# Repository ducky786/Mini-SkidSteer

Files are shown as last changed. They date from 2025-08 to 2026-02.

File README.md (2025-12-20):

# DESK TOP SKIDSTEER

My project is a small RC skidsteer for the desktop to cure bordom. This Skidsteer is around 80mm x 70mm with a arm that includes a bucket tilt. The arm and the Tilt are powered by servos while the drive bace is powered by 2 N20 motors. The 
I wanted to build this beucase I found an intrest in these small desktop toys that could be fun to kill time on your desk. I went for a skidsteer because it would consist of something more then just simply driving around on top of your desk.  Like picking up small
things and throwing them around. Another reason I wanted to build this was beucase I also wanted to learn something new! During this build I have defenetly learn a significant amound of cad and PCB design! But the main reason is to have pure fun with a mini constuction vehicel!! 
# CAD:





The wheels are place holders for a 26mm D-ring Wheels: [Wheels](https://www.amazon.com/10pcs-D-Hole-Rubber-Wheel-Suitable/dp/B0DHS12GDV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)

# PCB:





# Wire-ring Diagram:



# FIRMWARE:



# BOM:

| Part | Quantity | Price  | Link |
|---|---|---|---|
| N20 Motors | 2(comes with 3) | $9.99  | https://www.amazon.com/Acxico-Micro-Motor-3V-6V-Gearbox/dp/B09DG3GCGK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 |
| Buck Converter | 1 | $1.33  | https://www.aliexpress.us/item/3256809224651081.html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 |
| DRV8833 | 1 | $2.24  | https://www.aliexpress.us/item/3256806906685301.html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"order"%3A"12"%2C"eval"%3A"1"%7D&pdp_npi=4%40dis%21USD%215.74%212.24%21%21%2141.08%2116.03%21%402103244617539962038712743e4150%2112000039378712005%21sea%21US%216395794669%21X&curPageLogUid=tkZwLZppvI4E&utparam-url=scene%3Asearch%7Cquery_from%3A&search_p4p_id=2025073114100314644857276615300003037063_2 |
| Servos sg90 | 2 | $3.98  | https://www.aliexpress.us/item/3256805909602108.html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"order"%3A"42"%2C"eval"%3A"1"%7D&pdp_npi=4%40dis%21USD%211.99%211.99%21%21%2114.27%2114.27%21%402103244817539963500562681e2fa1%2112000035720830774%21sea%21US%216395794669%21X&curPageLogUid=MTCLJAN4xnVc&utparam-url=scene%3Asearch%7Cquery_from%3A&search_p4p_id=20250731141230268300773175950003082043_1 |
| Wheels | 4(comes in 10)  | $6.73  | https://www.amazon.com/10pcs-D-Hole-Rubber-Wheel-Suitable/dp/B0DHS12GDV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 |
| Xiao ESP-32 | 1 | $4.43  | https://www.aliexpress.us/item/3256806898073871.html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"order"%3A"667"%2C"eval"%3A"1"%7D&pdp_npi=4%40dis%21USD%217.93%214.43%21%21%2156.74%2131.69%21%402103246617539966920224373e09d8%2112000039345574623%21sea%21US%216395794669%21X&curPageLogUid=fVxbMNHtmWwP&utparam-url=scene%3Asearch%7Cquery_from%3A&search_p4p_id=202507311418121917005778551220003052960_1 |
| XT30 | 1 | $1.99  | https://www.aliexpress.us/item/3256808022842675.html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"order"%3A"868"%2C"eval"%3A"1"%7D&pdp_npi=4%40dis%21USD%213.36%211.99%21%21%2124.07%2114.26%21%402101ea8c17539968895486921e633c%2112000044241722915%21sea%21US%216395794669%21X&curPageLogUid=UwLOdHYcZP7Q&utparam-url=scene%3Asearch%7Cquery_from%3A&search_p4p_id=202507311421295032891313211630003124381_5 |
| Pin Headers | 1 | $2.79  | https://www.aliexpress.us/item/3256805730789728.html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"order"%3A"45"%2C"eval"%3A"1"%7D&pdp_npi=4%40dis%21USD%212.97%212.79%21%21%2121.23%2119.96%21%402101c80217539969536874429edd11%2112000034840648426%21sea%21US%216395794669%21X&curPageLogUid=ouSfWTDoT1n5&utparam-url=scene%3Asearch%7Cquery_from%3A&search_p4p_id=202507311422337454539819102040003087391_2 |
| Female Header | 1 | $0.72  | https://www.aliexpress.us/item/2251832677159829.html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"order"%3A"5"%2C"eval"%3A"1"%7D&pdp_npi=4%40dis%21USD%210.76%210.72%21%21%210.76%210.72%21%402101c5bf17539970477882420ed5c5%2165355679105%21sea%21US%216395794669%21X&curPageLogUid=lampIYBHwC27&utparam-url=scene%3Asearch%7Cquery_from%3A |
| Screw Terminal | 1 | $3.24  | https://www.aliexpress.us/item/3256804481581777.html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"order"%3A"238"%2C"eval"%3A"1"%7D&pdp_npi=4%40dis%21USD%212.84%211.99%21%21%212.84%211.99%21%402101c59817539971308151068e26ea%2112000030040613013%21sea%21US%216395794669%21X&curPageLogUid=c4xiFsyJKPl5&utparam-url=scene%3Asearch%7Cquery_from%3A&search_p4p_id=2025073114253012899010225579360003107920_1 |
| TATTU lipo | 1 | $15.99 | Amazon.com: Gens ace 7.4V 450mAh 2S LiPo Battery Pack 25C/50C with JST Plug for Emax Babyhawk RC Heli 250 Helicopter Small Airplane Micro FPV Racing Drone Quadcopter : Toys & Games |
| Motor Mount | 2 | $6.49  | https://www.amazon.com/MECCANIXITY-Mounting-Bracket-11-5mm-Screws/dp/B09NN6FQ78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 |
| 3D Print Shipping | | ~$10 | |
| PCB | 1 | ~$15 | |
| TOTAL | | 79.92  | |

# FINAL PRODUCT:

This is the final PCB design! I feel that it came out Great and what I love about this PCB is that I can remove it from the Skidsteer and place it into a 3d printed car! I plan on using this it on other projects.




Now the skidseer interms of CAD, it came out great too. There defenety have been some bad tolerences and alignment but it came together well enough.

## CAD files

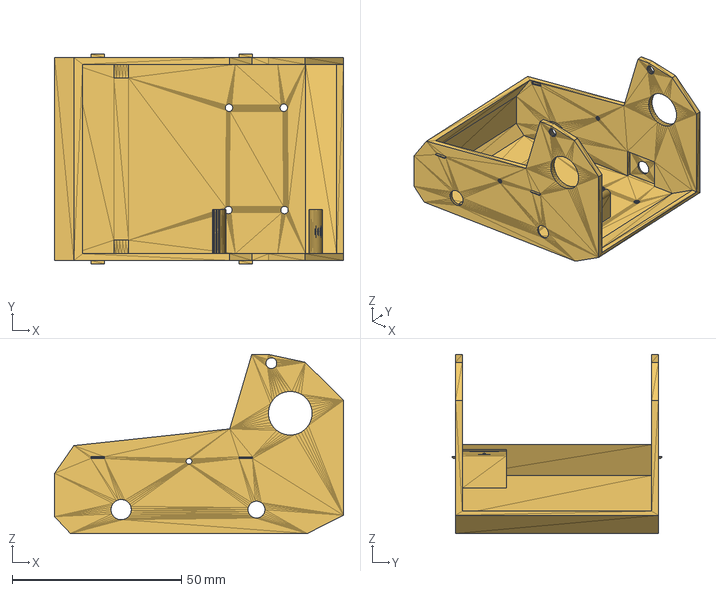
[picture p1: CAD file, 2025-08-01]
CAD/Body.step
85.4 x 62.0 x 53.0 mm

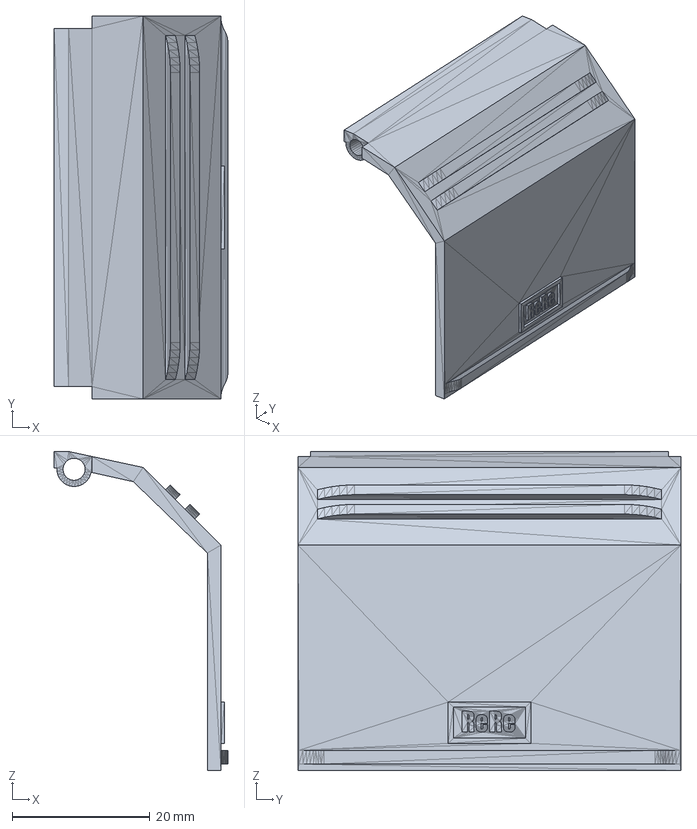
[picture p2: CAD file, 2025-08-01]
CAD/Back Cover.step
25.2 x 55.6 x 46.3 mm

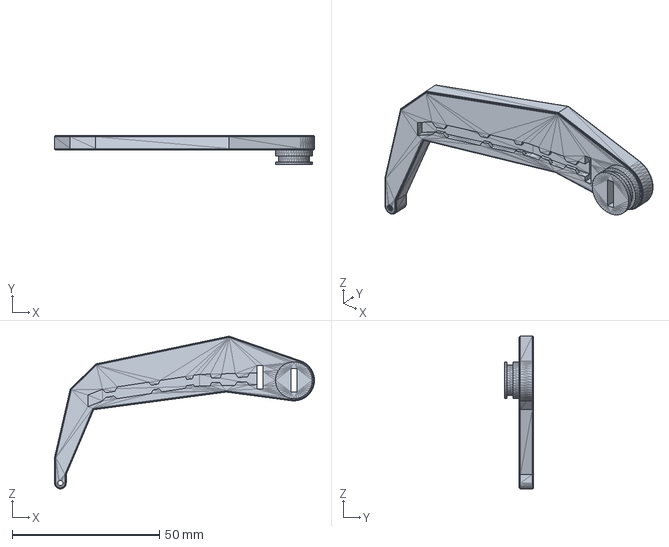
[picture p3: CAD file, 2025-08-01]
CAD/Right Arm.step
88.3 x 10.0 x 51.9 mm

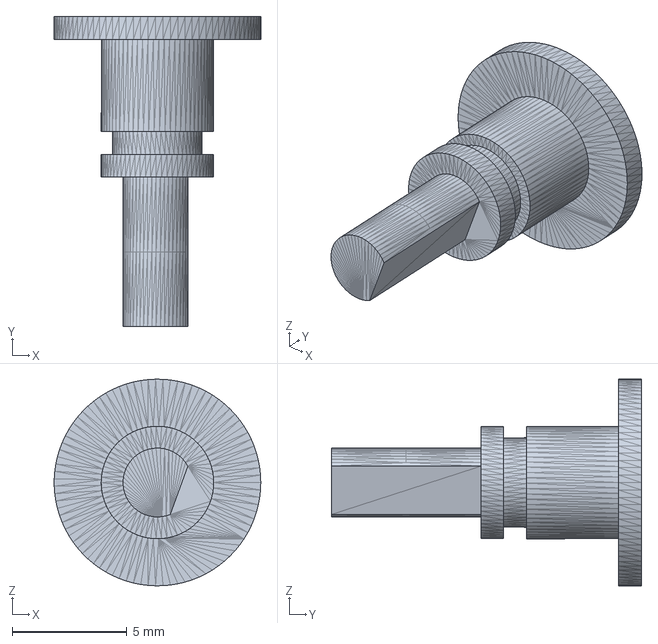
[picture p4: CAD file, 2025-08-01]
CAD/Axel.step
9.00 x 13.5 x 9.00 mm

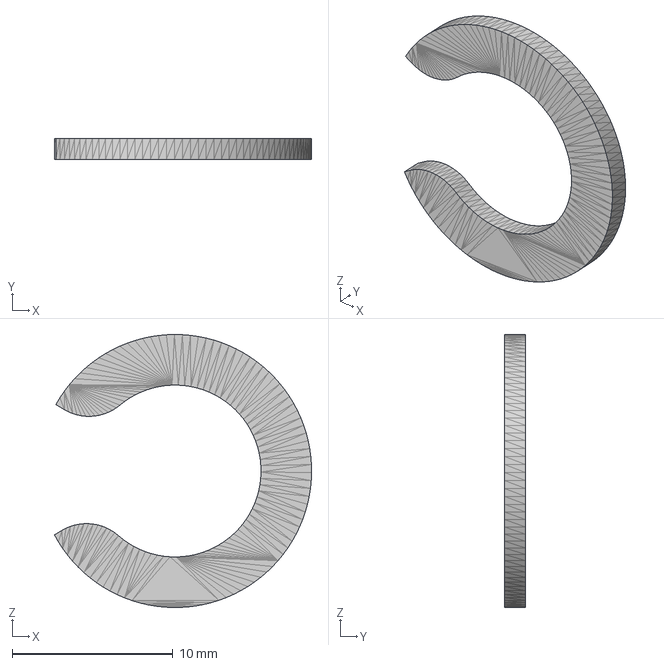
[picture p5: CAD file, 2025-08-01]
CAD/Arm C-Clip.step
16.0 x 1.30 x 17.0 mm

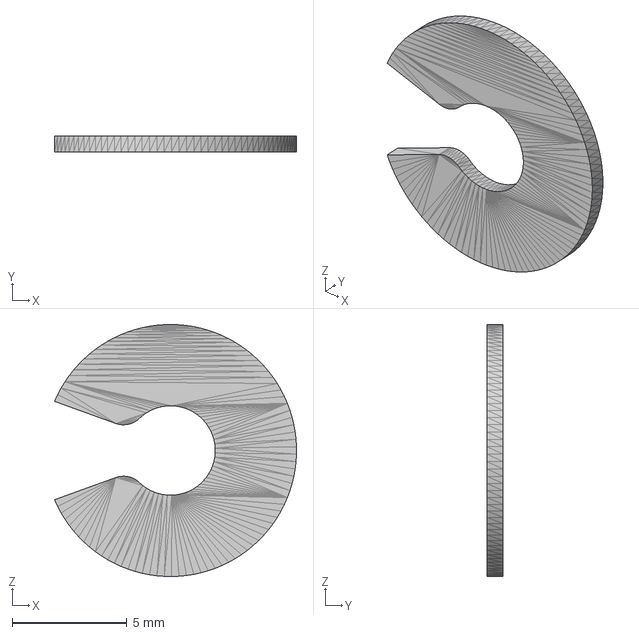
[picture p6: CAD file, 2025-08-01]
CAD/Axel C-Clips.step
10.6 x 0.7 x 11.0 mm

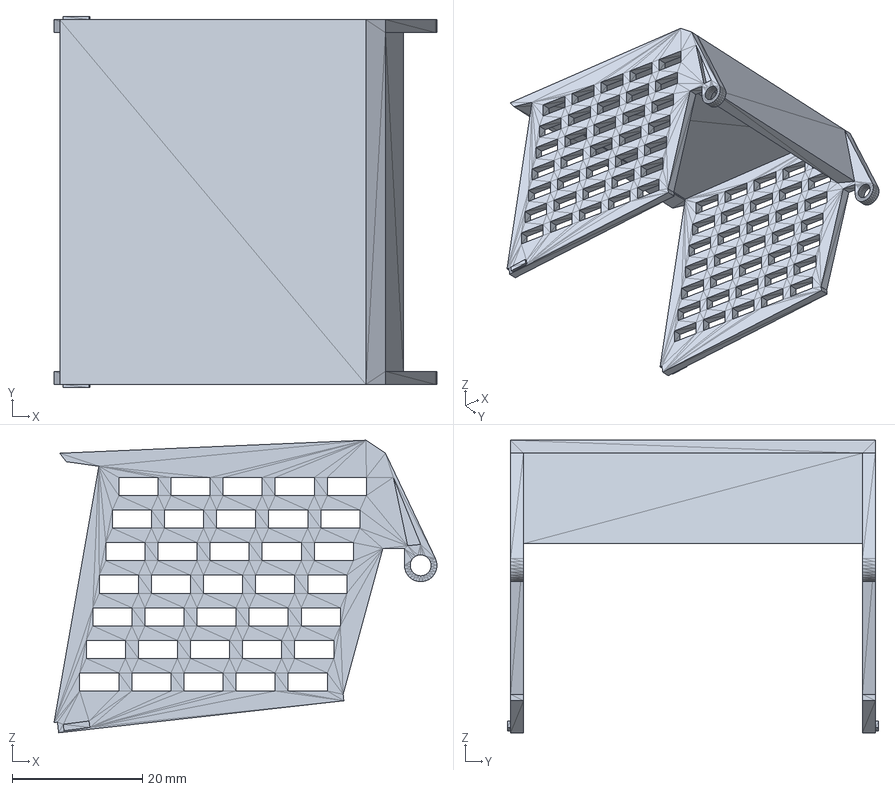
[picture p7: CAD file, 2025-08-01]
CAD/Driver Cab.step
58.8 x 57.0 x 44.9 mm

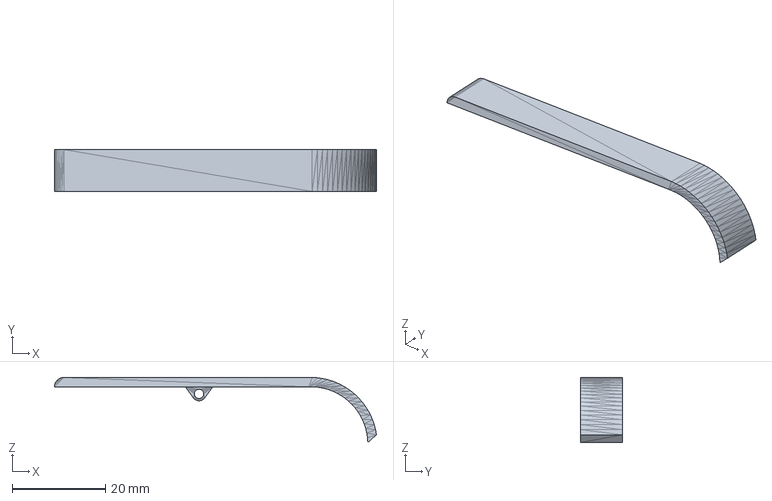
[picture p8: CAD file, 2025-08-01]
CAD/Left Wheel Cover.step
69.2 x 9.00 x 14.0 mm

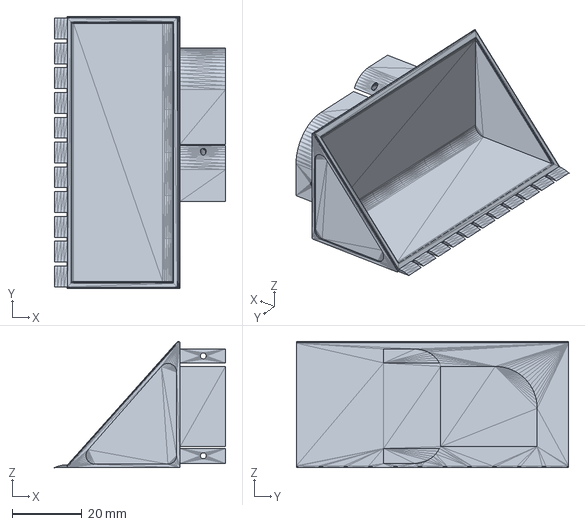
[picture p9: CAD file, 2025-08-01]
CAD/Bucket.step
49.0 x 78.0 x 36.2 mm

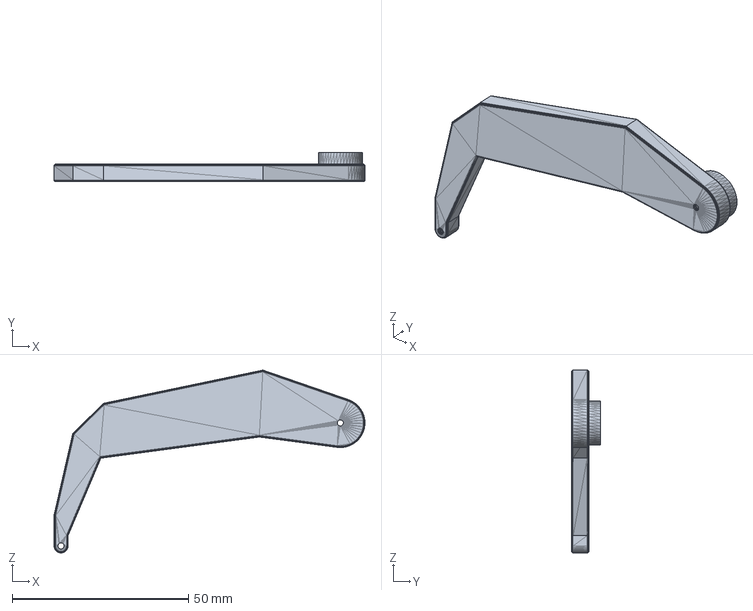
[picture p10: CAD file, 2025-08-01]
CAD/Left Arm.step
88.3 x 8.30 x 51.9 mm

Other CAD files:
CAD/Right Wheel Cover.step
CAD/Axel C-Clip E.step

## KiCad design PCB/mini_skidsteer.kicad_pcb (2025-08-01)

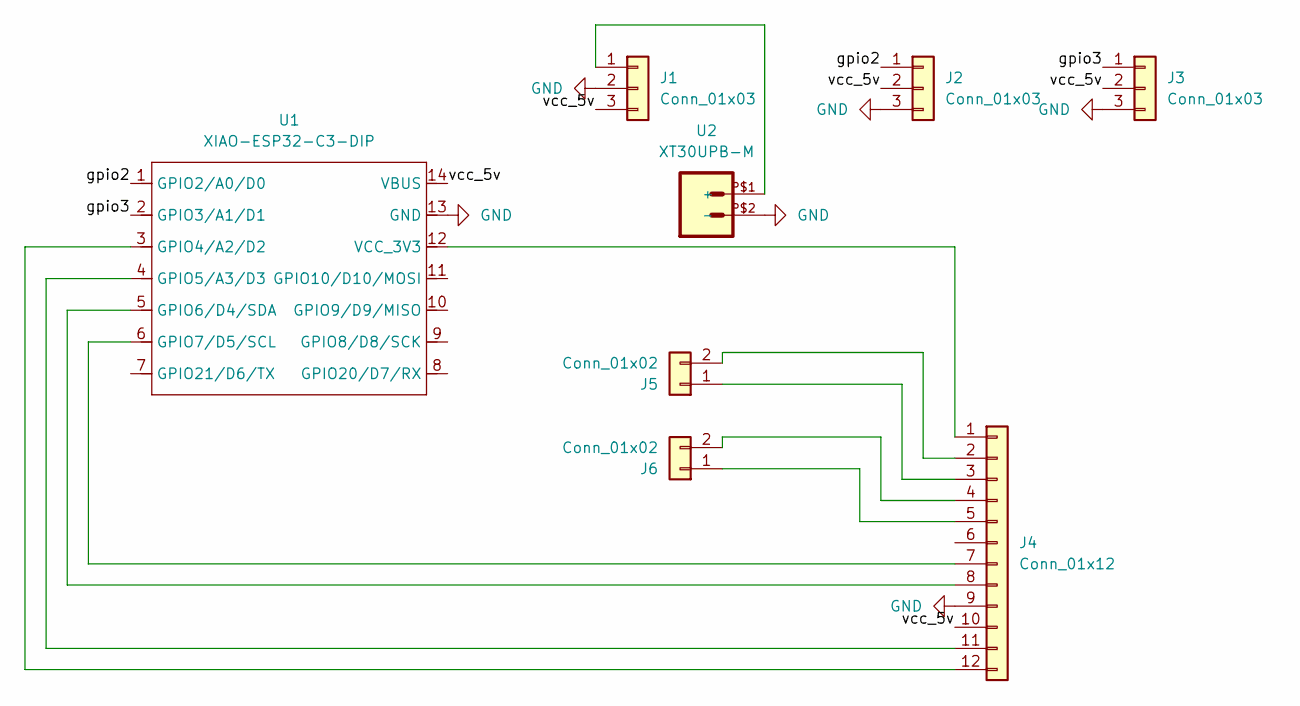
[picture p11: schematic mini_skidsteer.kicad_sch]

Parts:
J1: Conn_01x03; PinSocket_1x03_P2.54mm_Vertical
J2, J3: Conn_01x03; PinHeader_1x03_P2.54mm_Vertical
J4: Conn_01x12; drv8833
J5, J6: Conn_01x02; Altech_AK300_1x02_P5.00mm_45-Degree
U1: XIAO-ESP32-C3-DIP; XIAO-ESP32C3-DIP
U2: XT30UPB-M

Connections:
/gpio2: J2.1, U1.1 (GPIO2/A0/D0)
/gpio3: J3.1, U1.2 (GPIO3/A1/D1)
/vcc_5v: J1.3, J2.2, J3.2, J4.10, U1.14 (VBUS)
GND: J1.2, J2.3, J3.3, J4.9, U1.13 (GND), U2.P$2 (-)
unnamed: J1.1, U2.P$1 (+)
unnamed: J4.1, U1.12 (VCC_3V3)
unnamed: J4.2, J5.2
unnamed: J4.3, J5.1
unnamed: J4.4, J6.2
unnamed: J4.5, J6.1
unnamed: J4.7, U1.6 (GPIO7/D5/SCL)
unnamed: J4.8, U1.5 (GPIO6/D4/SDA)
unnamed: J4.11, U1.4 (GPIO5/A3/D3)
unnamed: J4.12, U1.3 (GPIO4/A2/D2)

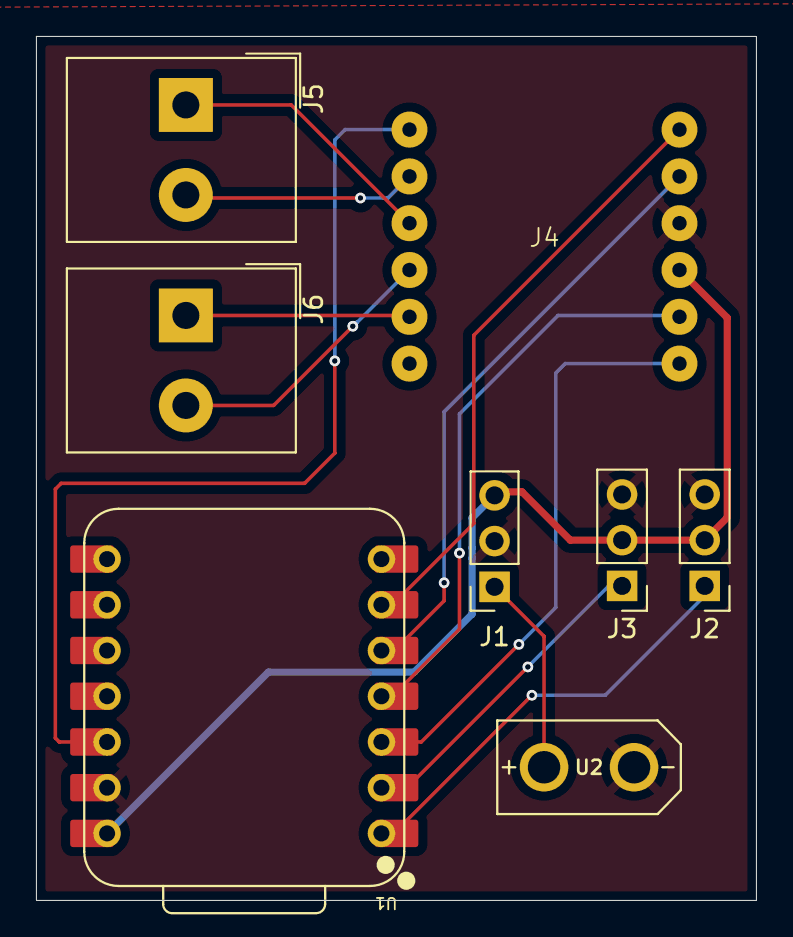
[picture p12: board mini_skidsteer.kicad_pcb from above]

Board: 2 copper layers, 40.0 x 48.0 mm, 8 parts (0 on the bottom side), 14 nets.

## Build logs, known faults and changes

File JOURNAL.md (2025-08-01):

---
title: "Mini SkidSteer"
author: "Rehan Shaik"
description: "Am creating a mini rc skidsteer for desktop to cure boredom"
created_at: "2025-07-2"
---

[Total Hrs Spent: 18hrs]

# July 8-9th: Started on CAD

Recently I have come accross many videos of rc construction toys. And one cought my eye. It was a skidsteer by professorBoots on yt! I thought it would be perfect to kill bordom on my desk. I started CADing creating the design that revolved around a similar design as professerBoots. I changed most of the functionality to reduce the complexity. Started with the body which for right now houses 2 N20 motors. The skidsteer will be driven as a tank drive so the motors will be mounted in the back and the front wheels will be mounted to 5x11x4mm bearing. The back cover and the cab are going to be screwed in together so they can swing open for easy access. I am really happy on the cad so far because this is my first time cading something that doesnt look entierly like a Box! I think the main body of the skidsteer is complete and all thats left to do is add the arm along with servo mounting points. After Cad is done I will have to start working on a costom PCB that can fit inside the small body!



Front Axel: The axel goes through bearings and cliped down to the body with a C-clip


[Time spent this session: 8Hrs]

# July 26-27: Finished CADing!!

I finally finished the CADing on my skidstear. I added the two arms and the bucket!. Both the arm and the bucket are powerd by 2 sg90 motors. I was consernced if the servo would be able to move the weight of the arm + the load so I added gears to increase the torque. The servo is connected to a 10 teeth gear wich drives a 22 teeth servo. 2.2 : 1 gear ratio. At the bucket, the connected servo controles the tilt of the bucket! The bucket is connect with 2M screws. The Right arm is connect with another C-clips, just like the axils in the front and the Left arm is connected with 2M screws which screw to the gear. Now that I have finished the CAD I am going to start on a PCB which will house the ESP-32, the motor dirvers and the battery! I am also considering on using LEDs to add a little more ummph to the Skidstear. After finishing the PCB I might also change the cab of the skid stear to inlude the tradintional holes that the actual skidsteers have.

Full design!


Bucket!


The Gears on the Arm!


The Right arm with the C-clip!


[Time spent this session: 4Hrs]

# July 30th: Finished PCB!

After long delay I finally finished my PCB!! I defenetly should not have pracasinated this long but I did! My PCB is 40mm x 48mm, I gave it a great amount of tolarace to I dont even have to think of it not fitting into my tiny tiny RC skidsteer! The brain of my RC skidsteer is a xiao esp32, with a drv8833 H Bridge for my my 2 n20 motors and a 5v buck converter. All of this is powerd by a TATTU 7.4v 300mAh 2S Lipo Battery. This is great for the small and compact size of this thing. During this process I struggled a lot on getting the right driver symboles and footprints for my drv8833 H Bridge so I got help from my cousin where we created custom footprint for it. Creating this PCB felt like hell because half the stuff I wanted, there were no footprints avalable or it was very difficly to find. But after a good hour of trying to find all the parts, I took a while looking up how to wire up the connesnts. This was second time ever creating a PCB so I felt very lost! But I did manage to get it done. I am still gonna go over and look at the pcb for any improvements or mistatakes to make sure this PCB turns out close to perfect as possible!

After creating the PCB I spent Some time on cleaning up my CAD design, like adding the holes in the cab to make it look cooler, adding the teeth to the bucket and changing the screw hole sides which I had all mixed up. I made the screw holes 1.7mm in diameter so I could simply screw them in with friction rather then heatsets. I felt doing it this way because from my last experiece in creating my macropad, the heatsets did not go so well and I thought it might ruin the skid steer. And after all that I think the CAD is offically complete so tmrw I can focus specifically on PCB and submitting!

PCB: 




CAD:


[Time spent this session: 5Hrs]

# July 31th: Made some experimental Code!

I Finsihed some of the experimental code for the skid steer. This is just the simple movement mechanism. Like forward, left and right. I am not really expecting this code to work just yet. I still have to add the core mechanism like the arm movement along with the bucket tilt! All of this I am hoping to create a UI for the controles where I will be able to controle the skidsteer through wifi on the ESP-32 Which I hope to set up very soon when I get the ESP32. This is driven using a tank drive, where the two back n20 motors work indpendently to move itselt forward or backwards or left or right! I have never coded for motors so it took me sometime to find something but I came across this nice video that kinda helped me understand things a little. I am honsetly still a bit confused on things but hey, I got something!

This is the experimental code not sure if this would acc work yet:


[Time spent this session: 1hr]

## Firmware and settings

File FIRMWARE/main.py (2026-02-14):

import network
import socket
import machine
import time
from servo import Servo
from RobotCar import RobotCar
# === MOTOR SETUP (DRV8833) ===
LEFT_1 =6
LEFT_2 = 7
RIGHT_1 = 4
RIGHT_2 = 5
motorPins = [LEFT_1,LEFT_2,RIGHT_1,RIGHT_2]
car = RobotCar(motorPins, 20000)
# === SERVO SETUP ===
armServo = Servo(pin=2)
bucketServo = Servo(pin=3)

# === MOTOR CONTROL FUNCTIONS ===

# === SERVO CONTROL ===

# === INITIALIZE ===
car.stop()  # prevent spin at startup

# === WIFI ACCESS POINT ===
ap = network.WLAN(network.AP_IF)
ap.active(True)
ap.config(essid='ESP32_Xiao_AP', password='12345678')
print("Access Point active at", ap.ifconfig()[0])
# === SOCKET SERVER ===
s = socket.socket(socket.AF_INET, socket.SOCK_STREAM)
s.bind(('', 8080))
s.listen(1)
print("Waiting for connection...")
conn, addr = s.accept()
print('Connected to', addr)
# === CONTROL LOOP ===
last_cmd_time = time.ticks_ms()
TIMEOUT_MS = 1000  # stop motors if no command for 1s
bucketPos = 0
armPos = 0
try:
    while True:
        conn.settimeout(0.05)
        try:
            data = conn.recv(1024)
        except OSError:
            data = None
        if data:
            cmd = data.decode('utf-8').strip().lower()
            print("Command:", cmd)
            last_cmd_time = time.ticks_ms()
            if cmd == 'w':
                car.move_forward()
            elif cmd == 's':
                car.move_backward()
            elif cmd == 'a':
                car.turn_left()
            elif cmd == 'd':
                car.turn_right()
            elif cmd == 'x':
                car.stop()
            elif cmd == 'armup':
                if not (armPos>=180):
                    armPos+=15
                armServo.move(armPos)
            elif cmd == 'armdown':
                if not (armPos<=0):
                    armPos-=15
                armServo.move(armPos)
            elif cmd == 'bucketdown':
                if not (bucketPos>=180):
                    bucketPos+=15
                bucketServo.move(bucketPos)
            elif cmd == 'bucketup':
                if not (bucketPos<=0):
                    bucketPos-=15
                bucketServo.move(bucketPos)
            elif cmd == 'stop':
                car.stop()
                armServo.move(0)
                print("Stopping program safely...")
                conn.send(b"Program stopping...\n")
                break   # exits while loop
            else:
                conn.send(b"Unknown command\n")
        # Safety timeout — stop if no command
        if time.ticks_diff(time.ticks_ms(), last_cmd_time) > TIMEOUT_MS:
            car.stop()
except Exception as e:
    print("Error:", e)
finally:
    conn.close()
    s.close()
    car.stop()

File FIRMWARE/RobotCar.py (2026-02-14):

from machine import Pin
from machine import PWM
import utime

'''
Class to represent our robot car
'''
class RobotCar:
    MAX_DUTY_CYCLE = 65535
    MIN_DUTY_CYCLE = 0
    def __init__(self, motor_pins, frequency=20000):
        self.left_motor_pin1 = PWM(Pin(motor_pins[0], mode=Pin.OUT))
        self.left_motor_pin2 = PWM(Pin(motor_pins[1], mode=Pin.OUT))
        self.right_motor_pin1 = PWM(Pin(motor_pins[2], mode=Pin.OUT))
        self.right_motor_pin2 = PWM(Pin(motor_pins[3], mode=Pin.OUT))
        # set PWM frequency
        self.left_motor_pin1.freq(frequency)
        self.left_motor_pin2.freq(frequency)
        self.right_motor_pin1.freq(frequency)
        self.right_motor_pin2.freq(frequency)
        
        self.current_speed = RobotCar.MAX_DUTY_CYCLE
        
    def move_forward(self):
        self.left_motor_pin1.duty_u16(self.current_speed)
        self.left_motor_pin2.duty_u16(RobotCar.MIN_DUTY_CYCLE)
        
        self.right_motor_pin1.duty_u16(self.current_speed)
        self.right_motor_pin2.duty_u16(RobotCar.MIN_DUTY_CYCLE)
           
    def move_backward(self):
        self.left_motor_pin1.duty_u16(RobotCar.MIN_DUTY_CYCLE)
        self.left_motor_pin2.duty_u16(self.current_speed)
        
        self.right_motor_pin1.duty_u16(RobotCar.MIN_DUTY_CYCLE)
        self.right_motor_pin2.duty_u16(self.current_speed)
        
    def turn_right(self):
        self.left_motor_pin1.duty_u16(RobotCar.MIN_DUTY_CYCLE)
        self.left_motor_pin2.duty_u16(self.current_speed)
        
        self.right_motor_pin1.duty_u16(self.current_speed)
        self.right_motor_pin2.duty_u16(RobotCar.MIN_DUTY_CYCLE)
        
    def turn_left(self):
        self.left_motor_pin1.duty_u16(self.current_speed)
        self.left_motor_pin2.duty_u16(RobotCar.MIN_DUTY_CYCLE)
        
        self.right_motor_pin1.duty_u16(RobotCar.MIN_DUTY_CYCLE)
        self.right_motor_pin2.duty_u16(self.current_speed)
        
    def stop(self):
        self.left_motor_pin1.duty_u16(RobotCar.MIN_DUTY_CYCLE)
        self.left_motor_pin2.duty_u16(RobotCar.MIN_DUTY_CYCLE)
        
        self.right_motor_pin1.duty_u16(RobotCar.MIN_DUTY_CYCLE)
        self.right_motor_pin2.duty_u16(RobotCar.MIN_DUTY_CYCLE)
        
    ''' Map duty cycle values from 0-100 to duty cycle 40000-65535 '''
    def __map_range(self, x, in_min, in_max, out_min, out_max):
      return (x - in_min) * (out_max - out_min) // (in_max - in_min) + out_min
        
    ''' new_speed is a value from 0% - 100% '''
    def change_speed(self, new_speed):
        new_duty_cycle = self.__map_range(new_speed, 0, 100, 40000, 65535)
        self.current_speed = new_duty_cycle

        
    def deinit(self):
        """deinit PWM Pins"""
        print("Deinitializing PWM Pins")
        self.stop()
        utime.sleep(0.1)
        self.left_motor_pin1.deinit()
        self.left_motor_pin2.deinit()
        self.right_motor_pin1.deinit()
        self.right_motor_pin2.deinit()
        
